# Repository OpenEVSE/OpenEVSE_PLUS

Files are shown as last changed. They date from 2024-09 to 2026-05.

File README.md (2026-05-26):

# OpenEVSE_PLUS
README.md for OpenEVSE Hardware
Files SCH and BRD in Eagle format
License CC BY-SA 3.0
OpenEVSE Hardware

Current Version OpenEVSE_PLUS_v6.5.1.

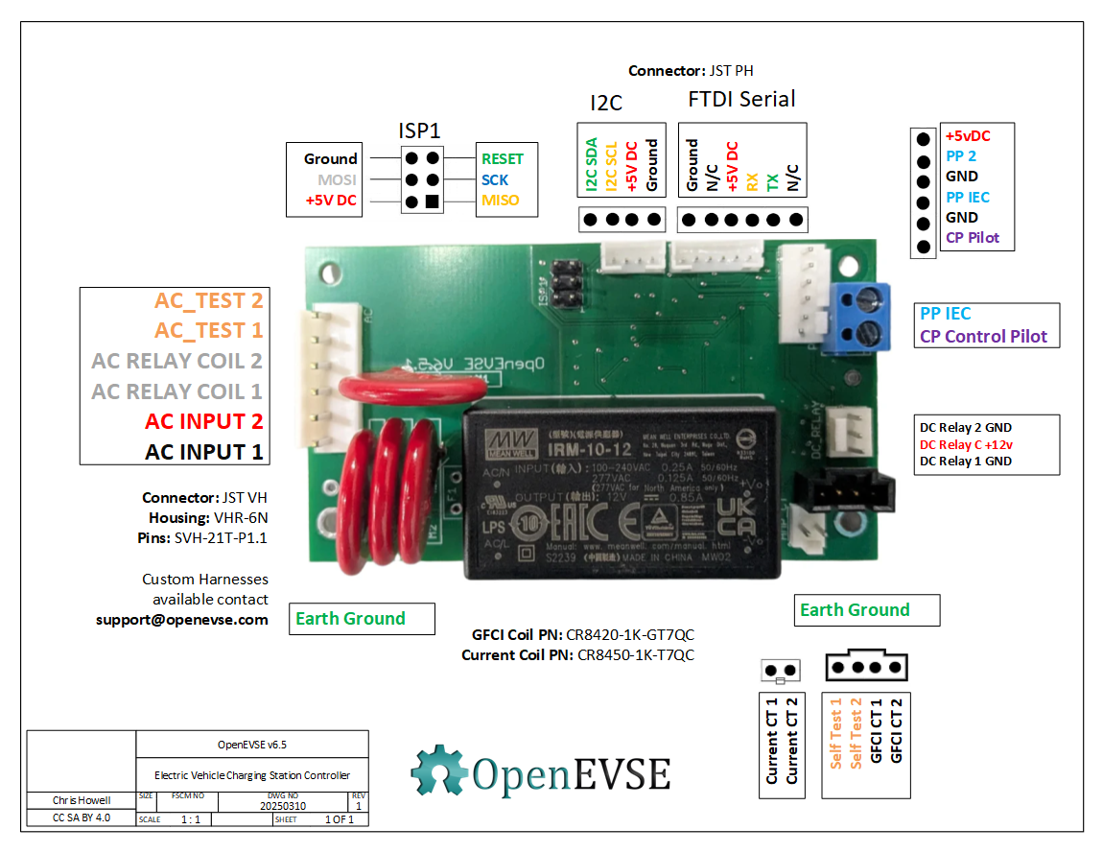
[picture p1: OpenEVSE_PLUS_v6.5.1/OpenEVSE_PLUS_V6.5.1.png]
OpenEVSE Electric Vehicle controller v5.5 SAE J1772 IEC 61851


OpenEVSE_PLUS_V6.5 - New more powerfull 10 watt Power supply (v5.5 and below 4 watt) with support for 277V AC and higher 85C operational temperature. Reworked AC detect circuits to support new UL requirement for "Continuous" Ground Monitoring vs "While Charging". Pulled ADC6 HIGH to auto detect CGMI requirement. Added on-board Surge supression MOVs. Added connector with Pilot, Proximity Pilot, Ground and 5v.

OpenEVSE Electric Vehicle controller v5.5 SAE J1772 IEC 61851

OpenEVSE_PLUS_V5.5 - Moved GFCI Test pin to enable move of DC Relay outputs to PWM capable pins supporting full power closing reduced power holding in OpenEVSE 7.1.2+ firmware. Pulled PD7 HIGH to auto detect board version in software to automatically set new/old pin values without requiring different firmware. Replaced 0.1" generic non-polarized connectors with JST PH for Serial (WiFi) and i2c (Display). Combined power and data connections for WiFi to reduce eliminate a screw terminal connector and simplify wiring harness. Replaced DC/DC converter with a TC1044S invert chip to generate -12v from +12v. 

OpenEVSE Electric Vehicle controller v5 SAE J1772 IEC 61851

OpenEVSE_PLUS_v5 - Optimized for reduced build time and high volume manufacturing of changing stations, removed most screw terminals and replaced with common connectors. Change from 2 single chanel opto-isolators for AC detection to 1 dual channel. Added ground connections to screw holes.

OpenEVSE Electric Vehicle controller v4 SAE J1772 IEC 61851

OpenEVSE_PLUS_v4 - Has 2 AC Detect chips like v1 + v2 plus the AC relay driver of v3. Added rectifier diodes to AC detect to improve detection in some conditions. Changed GFCI to individual pinout 4 pins.

OpenEVSE_PLUS_v3 - Removed 1 AC Detect chip and added AC relay driver. Added Current measurement circuit

OpenEVSE_PLUS_v2.5 - Added Current measurement circuit.

OpenEVSE_PLUS_v2 - modified GFCI pinout

OpenEVSE_PLUS_v1 - Inital version - Combined OpenEVSE v7 board and Advanced power supply into single board

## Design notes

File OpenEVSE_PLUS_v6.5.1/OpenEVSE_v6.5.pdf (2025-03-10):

## I2C FTDI Serial ISP1

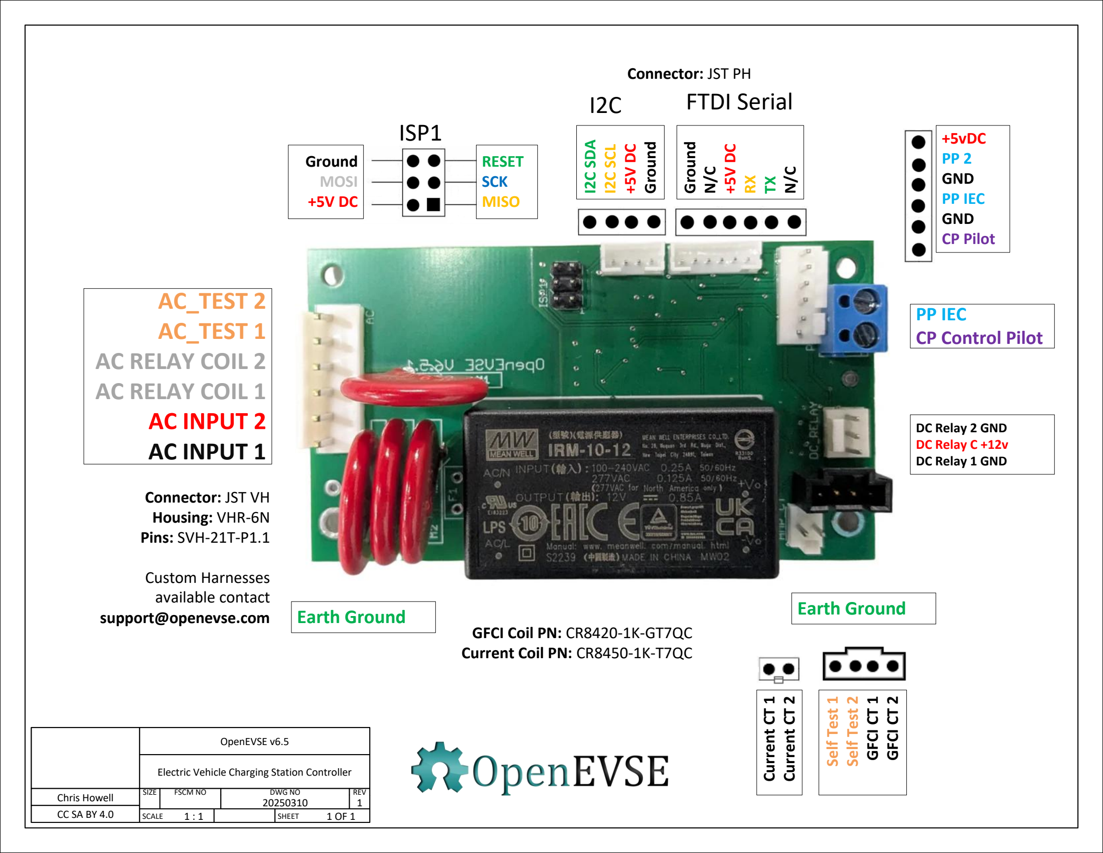
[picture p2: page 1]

Chris Howell Chris Howell | SIZE SIZE | FSCM NO FSCM NO | DWG NO DWG NO | REV REV
| | | 20250310 20250310 | 1 1
CC SA BY 4.0 CC SA BY 4.0 | SCALE SCALE | 1 : 1 1 : 1 | | SHEET SHEET | 1 OF 1 1 OF 1

OpenEVSE v6.5

Electric Vehicle Charging Station Controller

OpenEVSE v6.5

Electric Vehicle Charging Station Controller

## AC_TEST 2 AC_TEST 1 AC RELAY COIL 2 AC RELAY COIL 1 AC INPUT 2 AC INPUT 1

PP IEC
CP Control Pilot

Earth Ground Earth Ground

DC Relay 2 GND
DC Relay C +12v
DC Relay 1 GND

I2C SDA
I2C SCL

+5V DC

Ground

Ground

N/C

+5V DC

RX
TX

N/C

RESET
SCK
MISO

Ground
MOSI
+5V DC

Current CT 1

Current CT 2
Self Test 1

Self Test 2

GFCI CT 1

GFCI CT 2

Connector: JST VH
Housing: VHR-6N
Pins: SVH-21T-P1.1

Custom Harnesses
available contact
support@openevse.com
GFCI Coil PN: CR8420-1K-GT7QC Current Coil PN: CR8450-1K-T7QC

+5vDC
PP 2
GND
PP IEC
GND
CP Pilot

Connector: JST PH

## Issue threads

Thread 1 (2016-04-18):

Pilot power supply voltages are not shown or shown wrong, improvements recommended

jerkey, 2016-04-18:
IC4, the op-amp in the Pilot section, is shown with its negative power supply pin labeled "GND" but it is actually connected to VOUT- from the DCDC converter, whose GND is connected to actual GND of the circuit.  Neither VOUT- nor VOUT+ are labeled with voltages, but I was able to look up the DCDC power supply "D107E" and find out that it produces -12 and +12 volts from a FIVE volt input supply.

However, "DCDC" the D107E is shown in the schematic to be powered with +12v (coming from U$1 the AC-DC power supply) which would fry it if you try it.  Since the part called "TVS" is a 13.6v Zener diode (I had to look this up) there is really no need for a seperate DCDC converter...

I recommend deleting most of the parts inside the "Pilot" box and using instead an IXDD604PI mosfet driver chip, which you power directly from the +12v supply from the AC-DC power supply.

I would update the schematic but I use KiCAD not Eagle so I would have to start over.

Thank you for publishing this design.

chris1howell, 2016-04-19:
Deleting the DCDC and circuitry is not possible, SAE J1772 requires the pilot signal to operate at +12v HIGH and -12v LOW. The charging station to verify an EV is present, which is performed by a "diode check" at -12v. Several SAE J1772 error stated require the pilot to be pulled to -12v.

The bi-derectional TVS +13.6 and -13.6 is for surge, static and other transient spikes not for voltage regulation.

Part D107E (for 5v input) and D117E (for 12v input) were discontinued several years ago. The current OpenEVSE PLUS v4 uses part MD112D-12 in the Bill of Materials.

The recommended modifications and MOSFET driver would result in a non-compliant SAE J1772 pilot signal. The current design is mature and fully complaint with 100% compatibility on all vehicles tested.

Closed 2016-04-19.

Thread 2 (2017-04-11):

Bill of materials not ok?!

micdre, 2017-04-11:
Hello,

I found out that the BOM list, genretated in Eagle, is not ok in version 4 and 3! (maybe other versions too)
Is there somewhere a good list.

Regards, Michel

chris1howell, 2017-04-11:
I will take a look at the Eagle generated BOM. Any information on what parts are not okay?

micdre, 2017-04-11:
Hello
Thanks!

IC2 is not a mega 8 but a 328P
IC3 is not a LMV358 but a LM358
IC4 is not a LMV358 bu a LF353
Maybe there's more...

Costs me a couple of parts....

Regards, Michel

Verstuurd vanaf mijn iPhone

Op 11 apr. 2017 om 21:39 heeft Chris Howell <notifications@github.com<mailto:notifications@github.com>> het volgende geschreven:

I will take a look at the Eagle generated BOM. Any information on what parts are not okay?

—
You are receiving this because you authored the thread.
Reply to this email directly, view it on GitHub<https://github.com/OpenEVSE/OpenEVSE_PLUS/issues/2#issuecomment-293377590>, or mute the thread<https://github.com/notifications/unsubscribe-auth/AaAt5OanwKMKgq3p1027xw1ZBOK7_In8ks5ru9btgaJpZM4M5xZF>.

chris1howell, 2017-04-11:
I updated the following part values so generic footprints report the correct part when exporting Eagle generated BOM.

IC2 value 328P
IC3 value LM358
IC4 value LF353
TVS value P6SMB16CA
D1 value AZ23C5V6-7-F

micdre, 2017-04-11:
In wich version of the board?

Verstuurd vanaf mijn iPhone

Op 11 apr. 2017 om 22:07 heeft Chris Howell <notifications@github.com<mailto:notifications@github.com>> het volgende geschreven:

I updated the following part values so generic footprints report the correct part when exporting Eagle generated BOM.

IC2 value 328P
IC3 value LM358
IC4 value LF353
TVS value P6SMB16CA
D1 value AZ23C5V6-7-F

—
You are receiving this because you authored the thread.
Reply to this email directly, view it on GitHub<https://github.com/OpenEVSE/OpenEVSE_PLUS/issues/2#issuecomment-293384871>, or mute the thread<https://github.com/notifications/unsubscribe-auth/AaAt5Kc0vCaPSEjiRwvulRwJArvykdhDks5ru91lgaJpZM4M5xZF>.

chris1howell, 2017-04-11:
V4.

On Apr 11, 2017 1:26 PM, "micdre" <notifications@github.com<mailto:notifications@github.com>> wrote:
In wich version of the board?

Verstuurd vanaf mijn iPhone

Op 11 apr. 2017 om 22:07 heeft Chris Howell <notifications@github.com<mailto:notifications@github.com><mailto:notifications@github.com<mailto:notifications@github.com>>> het volgende geschreven:

I updated the following part values so generic footprints report the correct part when exporting Eagle generated BOM.

IC2 value 328P
IC3 value LM358
IC4 value LF353
TVS value P6SMB16CA
D1 value AZ23C5V6-7-F

—
You are receiving this because you authored the thread.
Reply to this email directly, view it on GitHub<https://github.com/OpenEVSE/OpenEVSE_PLUS/issues/2#issuecomment-293384871>, or mute the thread<https://github.com/notifications/unsubscribe-auth/AaAt5Kc0vCaPSEjiRwvulRwJArvykdhDks5ru91lgaJpZM4M5xZF>.

—
You are receiving this because you modified the open/close state.
Reply to this email directly, view it on GitHub<https://github.com/OpenEVSE/OpenEVSE_PLUS/issues/2#issuecomment-293389832>, or mute the thread<https://github.com/notifications/unsubscribe-auth/ABvYH50hh1Q3WBz-j6e3Ijn0WjQ5jKeUks5ru-HxgaJpZM4M5xZF>.

micdre, 2017-04-11:
Thanks!

Verstuurd vanaf mijn iPhone

Op 11 apr. 2017 om 22:34 heeft Chris Howell <notifications@github.com<mailto:notifications@github.com>> het volgende geschreven:

V4.

On Apr 11, 2017 1:26 PM, "micdre" <notifications@github.com<mailto:notifications@github.com><mailto:notifications@github.com>> wrote:
In wich version of the board?

Verstuurd vanaf mijn iPhone

Op 11 apr. 2017 om 22:07 heeft Chris Howell <notifications@github.com<mailto:notifications@github.com><mailto:notifications@github.com><mailto:notifications@github.com<mailto:notifications@github.com>>> het volgende geschreven:

I updated the following part values so generic footprints report the correct part when exporting Eagle generated BOM.

IC2 value 328P
IC3 value LM358
IC4 value LF353
TVS value P6SMB16CA
D1 value AZ23C5V6-7-F

—
You are receiving this because you authored the thread.
Reply to this email directly, view it on GitHub<https://github.com/OpenEVSE/OpenEVSE_PLUS/issues/2#issuecomment-293384871>, or mute the thread<https://github.com/notifications/unsubscribe-auth/AaAt5Kc0vCaPSEjiRwvulRwJArvykdhDks5ru91lgaJpZM4M5xZF>.

—
You are receiving this because you modified the open/close state.
Reply to this email directly, view it on GitHub<https://github.com/OpenEVSE/OpenEVSE_PLUS/issues/2#issuecomment-293389832>, or mute the thread<https://github.com/notifications/unsubscribe-auth/ABvYH50hh1Q3WBz-j6e3Ijn0WjQ5jKeUks5ru-HxgaJpZM4M5xZF>.

—
You are receiving this because you authored the thread.
Reply to this email directly, view it on GitHub<https://github.com/OpenEVSE/OpenEVSE_PLUS/issues/2#issuecomment-293391892>, or mute the thread<https://github.com/notifications/unsubscribe-auth/AaAt5HFzgKjKpxOICllg82zijdx22NiBks5ru-PFgaJpZM4M5xZF>.

Closed 2017-04-11.

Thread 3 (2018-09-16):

D8 Diode type

mr-const, 2018-09-16:
I found out in the BOM, that D8 diode value is 1N4004, but "device" name is  MBRA340T3, so it's not clear which one is valid, or they both can be used (1N4004 is 400V diode, however 340 is 40V only)

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

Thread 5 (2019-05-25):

Math / Theory of the GFCI circuit

RyanCopley, 2019-05-25:
I did find the theory of operations, and I reviewed the burden resistor calculator, but I am at odds with trying to understand how a burden resistor of 412 ohms was selected.

For the CT being used (http://www.crmagnetics.com/Assets/ProductPDFs/CR8400%20Series.pdf) it has the specs
Max RMS Current / Ir = 20 amps
Current Sensor turn ratio / Te = 1011:1
The arduino System Voltage is 5v

I plug these values in to https://tyler.anairo.com/projects/open-energy-monitor-calculator and I get a burden resistor of 89 ohms. Are you scaling down the max RMS current to ~4.3 amps for more sensitive detections?

Could you also go into explaining what the first OP Amp is for? I understand why the second one exists, but the first is elusive to me. My current guess is that it's being used as memory to keep an unbalanced current to remain a high value even whilst it oscilates

I would really appreciate the help understanding the theory here :-)

chris1howell, 2019-05-26:
The coil is scaled way down, there is no point reading anything over 20ma.
Sensitivity to low currents is more important.

The first stage of the Opamp is a amplifier or multiplyer. The input which
is a very tiny voltage is amplified before hitting the second stage which
is a voltage comparator. If the amplified voltage from the coil is above
the threshold the output of the opamp goes high. The Inturupt on the
microprocessor is triggered on the rising voltage of the opamp output.

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

RyanCopley, 2019-05-26:
Thank for you for the explanation, that is really helpful!

Closed 2019-05-26.

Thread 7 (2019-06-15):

Suggestion

jbakuwel, 2019-06-15:
Replace contactor with something like https://www.digikey.com/product-detail/en/sensata-crydom/D24125/CC1143-ND/254192

Zero-cross might also be nicer for the car charger....?

chris1howell, 2019-06-15:
Solid State Relays are not a good fit for EVSEs for 3 main reasons. The
main purpose of the EVSE is isolation until all safety checks pass. SSRs
can not guarantee isolation and there is a chance of shock even when
commanded off. Additionally EVSEs must fail safe. SSRs tend to fail closed
shorted where the mechanical properties of a relay tend to fail safe.

Additionally, SSRs have a pretty high internal resistance, at a high
sustained current this can translate into hundreds of watts of waste heat,
far too much to deal with in a small enclosure.

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

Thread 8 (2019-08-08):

Non OpenESVE LCD

samigroup, 2019-08-08:
Hello,
I am experiencing around with the OpenEVSE Plus Controller, I have added my available LCD 16X2, with pack module for I2C is there any way to update the I2C address without flashing the OpenEVSE controller code?
-- I know the LCD through the OpenEVSE is jumped A0-A2, so I soldered the A0-A2 jumpers to get the same address,  but its not just that, its more, where its two different communication schemes. But its protected for throught the header files and headers, I was wondering if I can change the selection of LCD definition/I2C header through the RPI interface (wifi interface)

- I am not using the RTC, nor the Temperature, ( disabled them through wifi interface)

samigroup, 2019-08-26:
If anyone was successful with this, it would be great if you can give me some pointers. Thanks!

chris1howell, 2019-08-26:
To use a different LCD/Controller combo you will need to modify the source
code to support your particular device and recompile.

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

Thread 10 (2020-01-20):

Suggestion for PP

giorgio80, 2020-01-20:
Dear,

I'm trying to maker hobby a board but it's  It's not clear pp specification. I better explain.
In particular,  it's clear for me how pp work,  simply reading resistance state to understand supported cable power and car presence,  but is not clear if it has to be 5v for specification.

I better explain.
I see it is connected to 5v then to add for reading inout.  My board works on 3.3v   so my question is :  would 3.3v setup would work or pp has to be 5v for j1772 specific ?

thanks.

sauttefk, 2020-01-20:
You can also use just 3.3V for your circuit. You just have to measure the resistance.
5V was the standard voltage of digital circuits back in the time, J1772 was standardized.

But 5V will have a higher noise immunity than just 3.3V, but i don't think that matters, as the resistance to measure is low enough (the current high enough).

Make sure to protect your PP input circuitry against static discharge and  leakage current due to wet/dirty ev-connector/short circuit to CP.

giorgio80, 2020-01-21:
Thanks for your answer, really more clear now . About checking the value can I also ask you when in the charging process it has to be checked ?
Thanks again :)

sauttefk, 2020-01-22:
You are developing a device that has a lot of inherent life threatening electrical safety risks!
Of course you have to monitor all values continuosly and shut off the power immediately when any parameter exceeds acceptable limits.
Maybe you should invest in getting the IEC61851 standard from ISO.

giorgio80, 2020-01-23:
hi @sauttefk
sorry I was not clear.  it's clear this has to be monitored continuously especially for overcurrent, real question was when PP has to be checked initially ,  I suppose immediately after pilot start ( and adapting load consequently) .  is this a right approach? I read around some other say that no Pwm pilot has to be started before pp is checked other instead say to start Pwm and continuously check for pp and to stop (without open contactor) charge process if no certified cable is detected.

Niko-La, 2020-01-30:
Make sure to protect your PP input circuitry against static discharge and leakage current due to wet/dirty ev-connector/short circuit to CP.

@sauttefk can you please elaborate on this.  Does openevse already do this in the schematic.

Also where can I follow the work being done for OpenEvse v6

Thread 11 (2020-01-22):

Incorrect GFCI self-test current?

davidrea, 2020-01-22:
The V5 schematic has a 330Ω resistor and 5V drive signal, resulting in a 0-15.15mA square wave through the self-test winding. The [CT product page](https://store.openevse.com/collections/all-products/products/gfci-current-transformer) indicates a trip current of 15-20mA, and a 5-turn self-test coil.

Should the resistor on the board actually be 1.6KΩ so that you only get 3mA through the self-test primary winding? In this case the voltage seen from the GFCI CT would be 5x that, since the nominal "pass the load wires through" case is a 1-turn primary. This would run the self-test at a current transfer ratio much closer to the design-intent in-use threshold.

(It's also understandable that there could be some CTR loss due to the crest factor of the square wave drive signal; the closest-to-ideal CTR would be with a sinusoidal input, so this might need to be derated a bit.)

chris1howell, 2020-01-22:
The UL current maximum for the test is 30ma. The test signal is not solid DC but PWM, the duty cycle is set to stay under the maximum.

UL has tested this setup with Wattzilla in the OpenEVSE v4 and are satisfied with the theoritialcal and tested levels.

Chris

On Wed, Jan 22, 2020, 1:40 PM Dave Rea <notifications@github.com<mailto:notifications@github.com>> wrote:

The V5 schematic has a 330Ω resistor and 5V drive signal, resulting in a 0-15.15mA square wave through the self-test winding. The CT product page<https://store.openevse.com/collections/all-products/products/gfci-current-transformer> indicates a trip current of 15-20mA, and a 5-turn self-test coil.

Should the resistor on the board actually be 1.6KΩ so that you only get 3mA through the self-test primary winding? In this case the voltage seen from the GFCI CT would be 5x that, since the nominal "pass the load wires through" case is a 1-turn primary. This would run the self-test at a current transfer ratio much closer to the design-intent in-use threshold.

(It's also understandable that there could be some CTR loss due to the crest factor of the square wave drive signal; the closest-to-ideal CTR would be with a sinusoidal input, so this might need to be derated a bit.)

—
You are receiving this because you are subscribed to this thread.
Reply to this email directly, view it on GitHub<https://github.com/OpenEVSE/OpenEVSE_PLUS/issues/11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>, or unsubscribe<https://github.com/notifications/unsubscribe-auth/AAN5QH3ZUFWEQT7AV622SYTQ7CHKFANCNFSM4KKKRWNA>.

davidrea, 2020-01-23:
Excellent, thanks for the clarification!

Closed 2020-01-23.

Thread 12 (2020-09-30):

GFCI tripping point.

faustomilletari, 2020-09-30:
Dear community,

According to this thread https://www.google.com/url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

there are changes in the regulation that require the GFCI to be more sensitive to current leakages. It seems that the current OpenEVSE hardware is built to have the GFCI trip at 15mA, whereas regulation requires 6mA.

I understand that changing the tripping point requires changes in the resitors used as burden resistor etc. I would like to ask you if
1) you think the current circuit can be adapted to the new requirements by swapping resistors
2) the new 6mA limit is high enough not to cause any issues with false positive tripping signals

I would like to state that i'm not an expert, and therefore i am still learning a lot. if i have misstated something in this issue please let me know and feel free to close it.

If also you could help me make calculations for new resistor values for the GFCI, in the sense of pointing me to material that can help me understand how that circuit works, i would be very grateful!

sauttefk, 2020-09-30:
**Caution:**
The current transformer used with OpenEVSE does not protect from **DC** fault currents.
Due to the fact that it is a coil around the conductors it can only pick up **AC** currents.

AC tripping current has to be at most 30mA
DC tripping current has to be at most 6mA

To achieve this you either need a Type B GFCI or a Type A GFCI plus something like the [WA RCM14-03 AC/DC Residual Current Monitor](https://deltrixchargers.com/wp-content/uploads/2019/10/WA-DS-015-RCM14-03-Rev-B.pdf).

A [hall effect sensor](https://en.wikipedia.org/wiki/Hall-effect_sensor) - in contrast to a current transformer coil - can detect DC current.

faustomilletari, 2020-09-30:
I am confused as of why this is needed at all... For a "normal" single or three-phase charging station where would we see this DC current coming from? The only place with DC current is the board itself and the pilot.

is this regulation meant to be applied by DC charging stations?

sauttefk, 2020-09-30:
A DC ground fault can occur, when a ground fault occurs behind the rectifier i.e. a battery pole has connection to earth.

faustomilletari, 2020-09-30:
Yes. now i understand. I am reading about it in this interesting article which says exactly what you stated in your last answer. http://www.mastrogippo.it/2019/09/rcm-direct-current-sensing-how-its-done/

thank you for helping me. It seems like this system is not required for EVSE meant to be home chargers for private use. So i think it might not be needed in my case...

thanks

SDCSolutions, 2020-09-30:
Looks like it is for the IEC62196 standard which governs CCS or DC charging. Also hence the loss of ground detect in the spec. http://www.doepke.co.uk/download/Techpub-06.pdf

Get Outlook for iOS<https://aka.ms/o0ukef>
________________________________
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

sauttefk, 2020-09-30:
**Attention:**
A DC ground fault can also occur with AC charging. A connection of the HV-battery to the chassis can easily happen e.g. a marten chewing on cables or rubbed through cables.

SDCSolutions, 2020-09-30:
So would that type of RCD need to be mounted on the ground line?

Get Outlook for iOS<https://aka.ms/o0ukef>
________________________________
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

sauttefk, 2020-09-30:
An affordable Type B RCD is this [GEYA GYL9 63A 30mA](https://de.aliexpress.com/item/33020060308.html)
An RCD is your life insurance when something bad happens to your EVSE / cable / connector / car in this wet, hot, cold, dirty environment you are going to deliver deadly voltages.

sauttefk, 2020-09-30:
When you do a 240V 2phase charging in North America, a 4 pole RCCB has to be used, leaving on pole unconnected (N/L1/L2/nc).

SDCSolutions, 2020-09-30:
Frank,
I guess my question is how is an RCD supposed to protect against a vehicle fault. Most of these control systems are designed to protect against unwanted electricity leaving the EVSE via the plug.

If I am understanding you correctly, this legislation is designed to protect against energy leaving the car?

Or is this in the event of a poorly set up solar panel installation?

Get Outlook for iOS<https://aka.ms/o0ukef>
________________________________
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

sauttefk, 2020-09-30:
A RCD monitors if any current sent out on one conductor does not return on any other conductor, but goes another way to earth. In the worst scenario through your heart.
So any insulation fault behind causing a current to earth, trips the RCD and therefore protects life and property.

A RCD can also be used to automatically isolate a faulty solar panel installation.

SDCSolutions, 2020-09-30:
Hi Frank,
I’m just trying to identify the source of the hazard here, the device that is being protected and the rationale of using it in a level 2 product.

If the source of the hazard is the vehicle, the RCD in the EVSE  is designed to protect the house?

I can understand the RCD being necessary for a solar panel, but then I question the rationale behind making the legislation around the EVSE as opposed to the solar panel.

If the hazard is the utility sending DC power,  along the same lines as the AC power, then I guess I would consider that a potentially valid risk. Not sure how it would happen as substations are usually all transformers where I live and it’s a little difficult to pass DC through them, but if I want to be protected from bad actors or negligent installations, why not make every plug an RCD circuit and leave the expensive hardware out of the EVSE.

Fundamentally, my question is why is this necessary to be put on a product people are already complaining is too expensive?

Get Outlook for iOS<https://aka.ms/o0ukef>
________________________________
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

sauttefk, 2020-10-01:
The International Electrotechnical Commission Standard [IEC 60364-7-722](https://webstore.iec.ch/publication/29958) demands either a 30mA Type B RCCB or a special Type EV (30mA AC/6mA DC) RCCB.

I don't know the legal requirements all over the world. But at least in Europe this is legally binding (every new installation has to obey these standards otherwise the electrician and/or the operator are liable for any damage or harm).
As far as I know these standards also apply to North Amerika.

chris1howell, 2020-10-01:
The standard in most of the world including USA is CCID 20. Which is AC
detection of ground fault at 20ma +0ma -5ma, so effectively the trip is
somewhere between 15ma and 20ma. There is no requirement for DC.

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

faustomilletari, 2020-10-02:
Hello,
thank you chris for your inputs.

I still hear conflicting opinions about this. I have found a component (datasheet here https://vacuumschmelze.com/Assets-Web/4641-X900.pdf) which has the desired functionality and is specifically built for EVSE.

Putting this component in the current design of OpenEVSE would mean to gut the GFCI portion of the circuit and simplifying it. Apparently PIN3 of the device linked above is low as long as there is no fault and goes in high-impedence whenever there is a system fault or a DC current >= 6ma or a AC current >= 30ma.

We could remove everything and add a pull up resistor to the GFCI_INT line connected directly to the pin 3 of the GFCI fault device linked above.

For what concerns tests. the devices wants to sense pin number 1 low (GND) for any time between 30ms to 1.2 sec to trigger testing. I would imagine GFCI_TEST line is active high, so i was thinking to put a NOT gate in tail of that line (with a pull up resistor just to make sure), and drive the PIN1 of the GFCI device with that.

The GFCI device absorbs around 35mA to function. Therefore i feel we can connect it to +5V and GND in the board.

Do you think such a change would work. I am NOT knowledgeable in terms of electronics, i'm improvising. i'm awaiting you expert opinion!

Fausto

faustomilletari, 2020-10-02:
Something like this? (I'm really confident this WON'T work)

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

sauttefk, 2020-10-02:
@faustomilletari  [benvac 4641-X900](https://vacuumschmelze.com/Assets-Web/4641-X900.pdf) is a very interesting part, but not cheap (~80USD ). Seems to be a product developed by Vaccumschmelze (ferrite and magnets) and [Bender](https://www.bender.de/produkte/differenzstrom-ueberwachung/rcmb121) (electrical safety products). The product name benvac stongly suggests this.

But [WA RCM14-03](https://www.stegen.com/en/ev-products/126-residual-current-sensor.html) seems to be cheaper (~60 USD) and easier to connect.

faustomilletari, 2020-10-03:
In that case, with WA RCM14-03, we would directly connect the GFCI_INT (active high) to the fault pin and GFCI_TEST (active high) to the test pin. The power supply would be directly the +12 GND form the AC/DC unit.

Great!

sauttefk, 2020-10-05:
[KEMET FG-R05-3A](https://content.kemet.com/datasheets/KEM_SE0217_FG.pdf) is also a possible AC/DC ground leakage current sensor (~60USD).

jackpotdk, 2020-11-16:
Aha!! @faustomilletari , I am sitting with the exact same challenge here.
I am currently looking at https://www.bender.de/en/products/residual-current-monitoring/rcmb121

Have you made any progress on the matter?

DeltaVetal26, 2020-12-03:
Hi all,

There is a similar sensor from Stegen Electronics (Netherlands).

https://www.stegen.com/en/ev-products/126-residual-current-sensor.html
It combines DC (6mA) and AC (30mA) leakage protection.

The only thing is that it requires an external 12V power supply and a logic level (for communicating with the controller) also 12V.

There are several options:

1) There is an I2C bus on the OpenEVSE board, which is not used, but its pins are on the terminal. In the firmware, you can configure these pins for input-output and connect a sensor to them (if the one that I suggested is through a voltage divider (for example, an optocoupler). It is impossible without a divider, since the microcontroller is not designed for 12V from the sensor.

 Then just read the state of the sensor pin. If a leakage occurs, the sensor will change the state of the line, we will see it and will be able to stop charging.

2) If you have OpenEVSE together with ESP (WiFi), you can also connect the sensor to it (via a divider). In it, poll the status of the sensor and, in the event of a leak, send a RAPI command to OpenEVSE to stop charging. But here you need to make sure that the ESP always has a connection with OpenEVSE in order to be ready to stop charging.

Closed 2020-10-02.

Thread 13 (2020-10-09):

e-Golf Charging keeps starting/stopping

arnolde, 2020-10-09:
I have a 2020 VW e-Golf since April 2020 (new) and have been charging it since May with OpenEVSE with 2 phases (it has a 7.2kW onboard charger), it worked fine until about a week ago, then the car was only charged sometimes, with interruptions. Today I sat down and finally had time for an extensive diagnosis, and I see the following:
a) once in a while I see "diode check failed" on the OpenEVSE webUI page (without the cable having been touched - when I soft-reset the EVSE with the RAPI command, it starts working again)
b) when no error is displayed, the car charges for about 10 seconds and then pauses for 10-30sec (the only way I see that is by logging the power meter every second and watching the current in realtime) - there is no regular pattern though, and it seems not to change behaviour when I change the charge current between 6/10/16A in the webUI - see the many narrow, square spikes in the image (ignore the long steady part in the left half, that is not the car)

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

c) after about 5 tries the car seems to stop trying to charge

The car's smartphone app sometimes says "I'm sorry, there was an error of some sort, and charging stopped". If I click on "start charging" then it starts (a new sequence of atempts) again.

If I charge the car with VW's own 230V-charger (ICCB) it charges fine.

The only other info I have, is that a couple months ago the openEVSE type 2 plug got wet (the cap was on, it was dangling with the cap downwards, it got rained on, which collected inside the cap) and the CP pin got corroded. I cleaned it a little and charging worked again, reliably, until about 1 week ago. When I started diagnosing the charging problem this morning, I cleaned it thoroughly, but it did not improve this whole issue.

It almost seems to me like the car's firmware was updated a week ago (over the air, without my knowledge) and now it doesn't work well anymore with openEVSE? Is that possible?

arnolde, 2020-10-11:
@chris1howell Maybe I should have opened this under open_evse ? I'm sorry I'm not sure where exactly the right place for such an issue is.

Is there a way to read a debug log in realtime (like per UDP broadcast i.e.) so I can see if the openEvse is even detecting the interruptions at all? (I don't have current sensors installed) - then I could be reasonably sure that the car is causing it, unless the PWM is failing for some reason...

chris1howell, 2020-10-11:
Github issues are generally for bugs in coding or errors in design. Support
requests should be sent to support@openevse.com.

A. Diode check error while unplugged sounds like water in the handle making
connection from pilot to ground. This could also cause GFI errors.

B. This issue sounds like a poor CP or ground connection or power is not
detected by the vehicle when the relay closes. Ensure the relay is closing
properly and power is provided to the vehicle.

On Sun, Oct 11, 2020 at 5:26 PM Ethan Arnold <notifications@github.com>
wrote:

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

arnolde, 2020-10-12:
Thanks! The diode check does not fail when unplugged, only once in a while when trying to charge. I have GFCI disabled since I don't have a GFCI transformer mounted, I rely on my 30mA GFCI in my house's main distributor box.

I guess I will have to monitor the PWM and relay contacts and report back with those results.

Is there really no event log with timestamps I could access, so I can see if there were any rapidly changing events I'm missing on the ESP webUI?

arnolde, 2020-10-29:
Just to conclude with this problem: I opened up the type 2 plug handle and found water drops inside. Apparently the plug was not watertight :-( after drying out everything for a couple days indoors and then with a hairdryer to be sure, I reassembled everything and it now works again. My suspicion is that the e-Golf EV detected false currents somehow and interrupted the charging.

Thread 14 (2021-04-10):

Advanced_v5_2020.pdf missing power regulator

kallisti5, 2021-04-10:
@chris1howell   The new Advanced_v5_2020.pdf diagram is missing the power regulator. It shows 12v connected to 5v directly

chris1howell, 2021-04-10:
The power regulator is not missing. The new (February 2020) OpenEVSE ESP32
WiFi board has a built in 12v to 3.3v DC/DC converter. It is much more
efficient and simple to wire than the previous UBEC/Huzzah setup with
external 12v to 5v converter and onboard 5v to 3.3v regulator.

On Sat, Apr 10, 2021, 6:06 PM Alex von Gluck IV ***@***.***>
wrote:

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

kallisti5, 2021-04-10:
oh.. Nice!  I just put the newer Feb 2020 board into my OpenEVSE and wired the wifi module up to the existing DC/DC converter.  Guess I need to crack it open and simplify a bit :-)

kallisti5, 2021-04-10:
although... the diagram does show 5v input pins on the wifi module which makes it a bit more confusing...
https://github.com/OpenEVSE/OpenEVSE_PLUS/blob/master/OpenEVSE_PLUS_v5/Advanced_v5_2020.pdf

SoDi1203, 2021-04-20:
hi, is this a broken link?
https://github.com/OpenEVSE/OpenEVSE_PLUS/blob/master/OpenEVSE_PLUS_v5/Advanced_v5_2020.pdf

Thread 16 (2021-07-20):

Connect LED to Open EVSE with free pin

DylanVautrin, 2021-07-20:
Hi !
After looking at this issue : https://github.com/lincomatic/open_evse/issues/98
I tried to connect RGBLED to open evse without I2C, so after looking for free pin , i've undefined the RGBLCD to use pin of the LCD in first time, but when i try to write a HIGH/LOW levels on pin SDA, the Open EVSE restart continually.
I used the shortcut "SDA" in the code.
Maybe i do something wrong, someone have a solutions or a different way to proceed ?
Thanks
PS: I just do a digitalWrite(SDA,HIGH);

Closed 2021-07-20.

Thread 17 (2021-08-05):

5.5 board support additional j1772 output?

sroskelley, 2021-08-05:
Seems like this board could support an additional j1772 with no new parts to the board.

posit1: Board already supports two dc contactors?
posit2: PP pin is connected to a pwm?
posit3: risk doesn't increase with this feature.

examples scenerios, A, B ,C.. pilot1 is PLT.. pilot2 is PP
Say controller is configured for <=32amp output for this example.
A, state: 0 cars connected.
A, contactor1, off
A, contactor2, off
A, pilot1: allows 16 amps
A, pilot2: allows 16 amps

A->B
B, car is connected to pilot1. Requests 16amp (per pilot advertisement)
B, contactor1, on
B, openevse detects amprage draw of ~16
B, pilot2 gets set to 1amp allowed.
B, pilot1 gets set to 31amp allowed.
B, contactor2, stays off

B->C
C, car gets connected to pilot2. Reqests 1amp  (per pilot advertisement)
C, pilot1 gets set to 16amp allowed.
C, wait for monitored amperage to be reflected to <16amps before enabling c2.
C, pilot2 gets set to 16amp allowed.
C, contactor1, on
C, contactor2, on

In all scenarios if amperage is ever detected to be over.. cut all contactors(just like now)

The only new part needed for the kit would be a contactor and j1772 assembly. No additonal coils. second j1772 would flow through same current sensors but differnet contactor.

I assume I'm missing something safety wise.. Sorry for wasting everyones time, unless someone learns something, then I regret nothing.

Side question.. is there there a reason we wouldn't move the coils to be on the input instead of the output of the 5.5 diagram

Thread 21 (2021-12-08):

Stuck relay

kallisti5, 2021-12-08:
Hey, the stuck relay detection works :-)

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

Had the 50A Struthers - Dunn contactor weld itself running at 32A.   Anyone else have issues like that?  The relay is only around a year old.

kallisti5, 2021-12-08:
Looks like a few other people have seen this:
https://groups.google.com/g/openevse/c/4wFzy82jwYo

kallisti5, 2021-12-08:
I lightly took a file to the contacts, then sanded with 400 grit, 2000 grit, and scrubbed the contactor with contact cleaner.
30A after 5 or 10 minutes and everything seems fine again without any excessive heat

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

We might want to add cleaning the contactor to yearly maintenance or something

kallisti5, 2021-12-08:
I'm working on a contactor maintenance guide here:
https://openevse.dozuki.com/Guide/Contactor+maintenance/40

I need to get a few more pictures together before it's ready to publish

kallisti5, 2021-12-08:
Published.  I changed the language from Contactor to Relay.  *Technically* these are more contactor-like vs relay-like, but the datasheet calls them relays... so I digress :-)

https://openevse.dozuki.com/Guide/Relay+Maintenance/40?lang=en

Closed 2021-12-08.

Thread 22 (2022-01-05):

CCS-Type 2 DC from DC Power?

JohnGalt1717, 2022-01-05:
Hi, I'm building a DC Bus design that skips the entire inverter process. Is there any documentation on using DC fast charging with this project?

Basically what I'm looking at doing is using this, if possible to charge from a LiFePO4 battery + solar directly DC with a small DC/DC synchronous boost converter (at over 98%) which will cost about 1/8th the cost of a dc/ac converter and eliminate all of the losses from DC/AC and then back AC/DC in the car. The synchronous boost converter is easy (going for 384VDC) and I've built one. The harder stuff that is more risky is to talk to the car and now blow up a $30K battery in the car.

Thanks!

zymurgic, 2022-10-20:
CCS protocol for DC is very different from the simple PWM protocols that OpenEVSE does for AC charging to communicate with the vehicle's on-board charger. For a start, it will communicate via a powerline network over the CP pin.  There's a lot of reading to be done of the official standards.

I wish you all the best of luck, it's not going to be easy.

JohnGalt1717, 2022-10-20:
A couple of things here just if anyone else is thinking about this problem:

1. Tesla I believe uses CANBus which should be MUCH easier to work with.
2. ST has full sample units on their site that will do charging over CCS. Considering buying one because they come without the DC/DC converter.  The problem then becomes not the car, but communicating with the ST board to tell it max current draw etc.

strohrbaugh, 2023-02-24:
I'm interested in doing something similar, too. Have you developed this any further?

JohnGalt1717, 2023-02-24:
I've found the following:

Tesla was using CAN but now uses Power Communications and indeed uses the same protocol as CCS.
There are off the shelf Power Communications systems.

The basic flow would be:

1. Plug in
2. Negotiate (PP, PE etc.)
3. Establish communication over IP
4. Talk via IP to negotiate voltage and amperage.
5. End if PP/PE or IP request.

Charger would be:

1. DC in. (or PFC to DC)
2. DC/DC boost (or buck depending)
3. MCU that talks over IP and Power Communication Protocol that controls the boost converter.
4. Various sense pins for PP and PE.

The hardest part of this is actually the IP link and coms.

JohnGalt1717, 2023-02-25:
You’re still losing dc to ac and then ac to dc doing this and if you use an off the shelf transformerless inverter you’re not going to gain a thing.

You’re at best at about 87% efficiency that way.

The reason to do dc/dc is that you can get into the 97-98% efficiency with a synchronous buck/boost.

strohrbaugh, 2023-02-25:
Oh I completely agree, but I haven't yet solved the comms problem that you articulated above. The DC-AC solution "solves" it, but admittedly quite poorly. Let you know if I come across any improvements using something approximately off-the-shelf.

JohnGalt1717, 2023-02-25:
There's a company that the Electric Viking on YouTube referenced that has a DC/DC charging solution coming.  I can't find anything about them.  But it's a lead.

strohrbaugh, 2023-02-25:
Thanks, that's a good start.

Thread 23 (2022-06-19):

Help identify OpenEVSE board

mat02, 2022-06-19:
Hi!
I have an OpenEVSE-based charger that I bought with the car. It's a DIY build, so I don't have any info about it. I would like to update the firmware and add WiFi module. Unfortunately, I am not sure which version of the firmware will be compatible with this board as I cannot find it anywhere in the Github repository. Can you please help me identify this board? Board is made out of two PCBs, the lower one is a 12V power supply, the upper one has uC and all the control pins.
Best regards,
Mateusz

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

martiinezz, 2022-06-19:
Skoro ma diodę to raczej kompatybilne z wersją 3 sprzętu. Która wersja FW obecnie tam siedzi?

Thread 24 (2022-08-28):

Short-circuit on AC output results in current transformer burden resistor failure.

kyang014, 2022-08-28:
During testing, I induced a short circuit on AC output of a OpenEVSE Advanced kit with controller hardware V5. The upstream circuit breaker tripped, but the event appears to have caused R26 to fail open. On subsequent charge attempts, the sensed current value was 100A+ despite the real current being 16A. Overcurrent faults were thrown as a result and charging stopped.

The current transformer itself tested normal and output a voltage corresponding to the correct 16A when measured out-of-circuit with a known good burden resistor. The 2.5V divider on the controller was also working.

The controller operates normally when R26 was replaced. Presumably, the spike of current through the CT during the short circuit induced a high voltage across the CT output. Suggest clamping the voltage across R26 to protect both it and the ATMEGA.

kyang014, 2022-08-28:
Potentially could be reproduced by using a bench power supply to apply a pulse of current to a wire wound around the CT many times to multiply the sensed current.

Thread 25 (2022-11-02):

Time to ditch the 328P for an RP2040 or something purchasable?

DrFrankReade, 2022-11-02:
Leaving the certification problem for another time.

I feel it's time for a hardware refresh, esp. a new MCU, and maybe spread the board out a bit.

Can't buy the Arduinos anymore. I would not be surprised if the ATmega328 is extinct. Digikey only shows "marketplace" products which are in all likelihood counterfeit or pulls.  Plus, the existing code barely fits.

I'm not kidding when I say we're using RP2040 at work in place of SAM chips we can't buy anymore, and always having a good laugh about it.  They require a few more external parts and they run at lower voltages, but they're impressive pieces of hardware with incredible community.

Stock has got to be running low on the existing OpenEVSE boards to boot.

doanerock, 2022-12-31:
I am confused because the only microcontroller on the OpenEVSE is a esp32.  Are you referring to the OpenEVSE Programmer, because I am pretty sure you can use any FTDI programmer, so this is a non issue.

DrFrankReade, 2023-01-02:
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

Every OpenEVSE has one.

It's where THIS code runs...

[https://github.com/OpenEVSE/open_evse](url)

doanerock, 2023-01-03:
You are correct, my bad.  I had to bring up the schematic to find where it is located.  Looks like it is under the relay which is why I could not find it in the pictures.
It looks like there are plenty of ATMEGA168P-20AU in stock.

DrFrankReade, 2023-01-03:
The 328 is the one that's shipping, and that's what the .bin releases are compiled for. The 168 also has half the program space, and if I recall correctly, the current code barely fits the 328.

My OPINION, aside from easing the supply chain concerns, is that a heftier MCU would give a bit more headroom to put back the old LCD based UI, which I think is gone nowm, and missed by me at least, for redundancy's sake, because it's been my experience that when the ESP32 goes down, the charger goes squirrely and I either can or can't charge the car.

Unfortunately, to move to a little ARM chip would require a complete hardware rework, as most stuff maxes out at 3.3V nowadays, and of course then supporting two hardware revisions... but if you can't buy chips, you can't ship product.

There are other ATMEGA 8 bit chips - The 32U4 seems to have a lot of stock, and it's a popular chip, and there's also something called a atmega4808 and somebody's written a core for it too, although I have no idea how well it works.

My thoughts anyway.

KanyonKris, 2024-04-14:
What a difference a year makes. While Microchip does not recommend the ATmega328P for new designs (https://www.microchip.com/en-us/product/atmega328p), it appears to be available for a reasonable price. Mouser has 90k in stock at $2.30 @ 100 qty.

The recommended successor, ATmega328PB is cheaper. It is not a drop-in replacement, there are 4 pin reassignments that will require a PCB revision, but 328 code will run on it. (https://www.pololu.com/file/0J1464/Atmel-42559-Differences-between-ATmega328P-and-ATmega328PB_ApplicationNote_AT15007.pdf)
Mouser has 33k of the extended temperature version in stock for $1.46 @ 100 quantity.

martiinezz, 2024-04-15:
Why not ESP32, it has 2 cores - WiFi and BT available - so it could be also possible to read cars battery state via BT to let say charge to 80 or 90% as some EVs lack such option.

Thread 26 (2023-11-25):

openevse terminal no longer detects cars

monfiston, 2023-11-25:
HELLO
my openevse terminal no longer detects cars
I can however modify parameters in the openevse
I tested the type 2 charging cable: ok
I tested that the CP pilot cable reached the openevse motherboard

do you have any idea which component would be hs on the openevse board?

Mathopenevse, 2024-01-22:
Salut, est-ce que tu as pu régler ton problème depuis? Ça m'ait arrivé déjà après avoir flashé la carte mais au bout de plusieurs essais c'est rentré dans l'ordre

monfiston, 2024-01-22:
Non

Mathopenevse, 2024-01-23:
Tu es sous quelle version? Tu as essayé de flasher ta carte?

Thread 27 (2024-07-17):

what is the different 5.6 board and 5.5 board

flyrobot, 2024-07-17:
i just realized the board i bought is version 5.6.
What is the difference between 5.5 and 5.6 ? is any documentation for 5.6 ? such as schematic, pcb, etc

Thank you

chris1howell, 2024-07-17:
There is no meaningful difference. The 2 larger ICs were moved from top (through hole) to bottom (surface mount) due to better part availability.

flyrobot, 2024-07-18:
is it possible to get 5.6 on github ? its quite difficult to trace the problem on the pcb's 5.6 base 5.5 kicad source

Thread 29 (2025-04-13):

6.5.1 I2C connector reversed?

ptrauejr, 2025-04-13:
In looking at the diagrams I see that on 5.5 the I2C connector had the key (open side) facing towards the edge of the board and the sda (green) was on the left.  On 6.5.1 I see that the I2C connector had the key facing away from the closest edge of the board yet the SDA was still on the left.  Was the connector reversed, or is this an oversight?

I'm upgrading from a 5.6 to 6.5.1 and l just want to make sure I hook this up properly.

leothehuman, 2025-09-07:
My kit also looks  like the kit pictured above. I also believe the connector is mislabeled in both png and pdf schematics.

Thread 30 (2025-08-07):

Kit Assembly Layout OpenEVSE_PLUS_v6.5.1

martin3142, 2025-08-07:
Very good kit, thanks.

**1:**

For the present backplate layout, there is overly generous space left at the top of the case compared to the overly difficult cramped area at the bottom that must accommodate the heavy gauge cables...

See my assembly attempt!

To make the cabling easier, can the OpenEVSE module and relay both be moved equally towards the top of the base plate to give more room for cabling in the lower 1/3rd of the case?

**2:**

I placed the temperature sensor on the relay to give early warning of any problems with a (hot) resistive connection on the high current side. This is close to exposed mains terminals: Hence the use of insulation tape around the terminals to protect for if the sensor were to become detached/loose.

Are shrouds available for the mains terminals?

Thanks,
Martin

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

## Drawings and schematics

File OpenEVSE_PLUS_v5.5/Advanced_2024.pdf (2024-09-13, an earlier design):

## 5v i2c

## LCD/WiFi

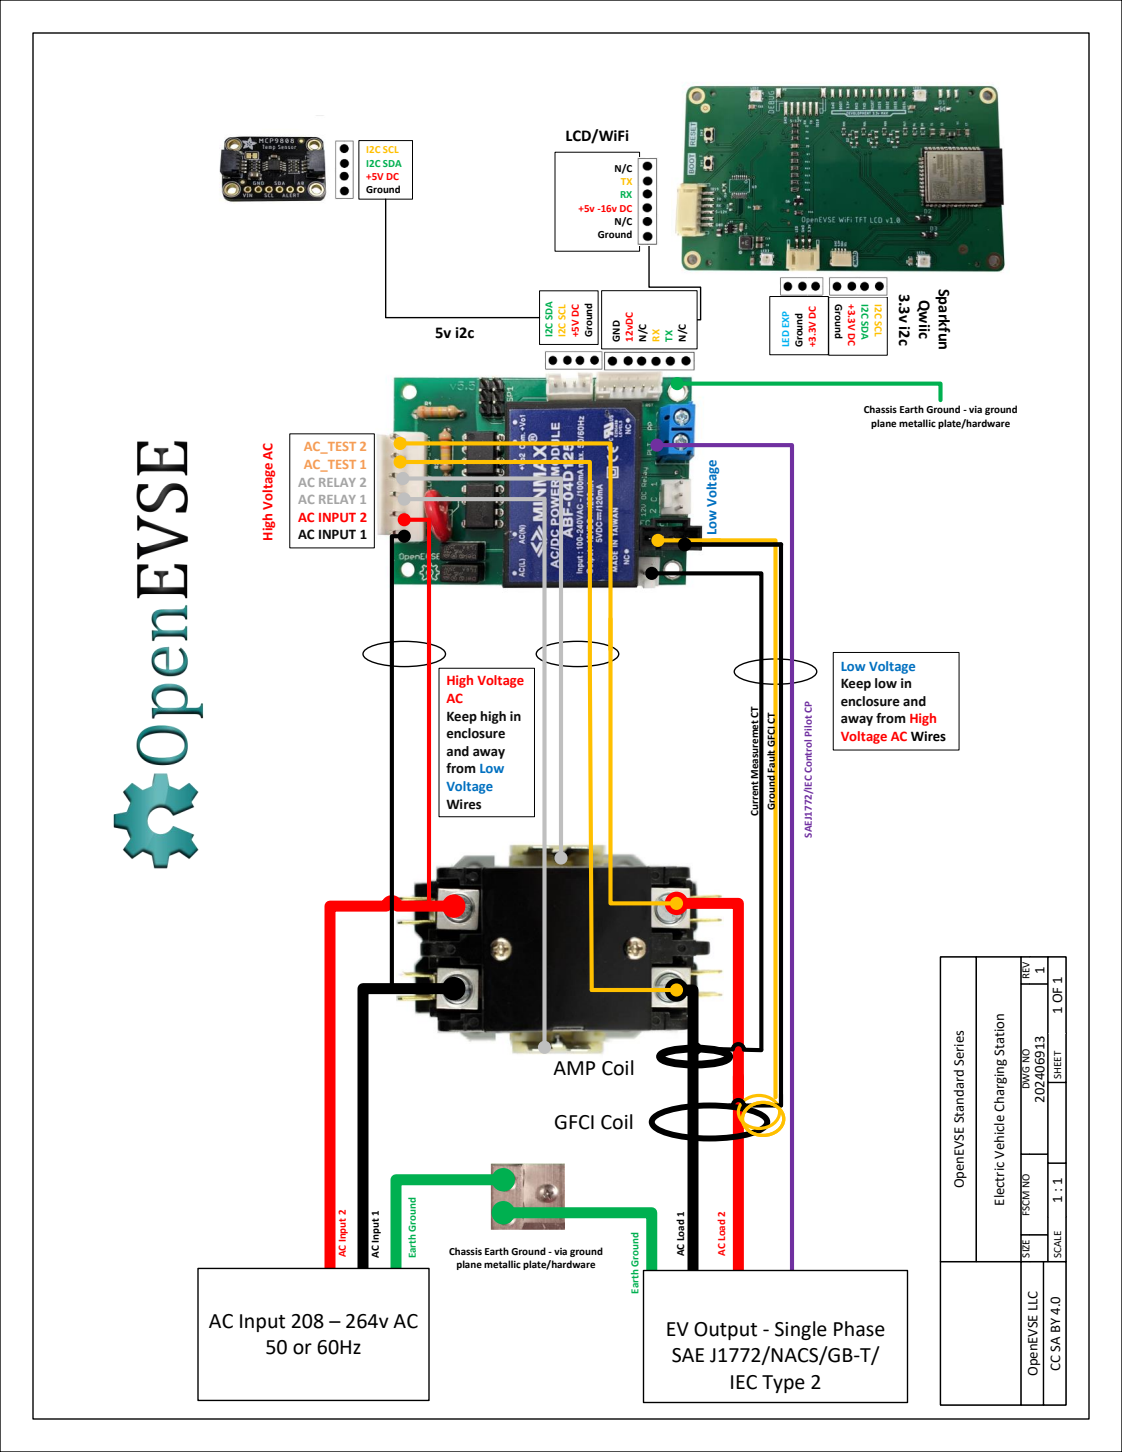
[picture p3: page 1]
I2C SDA; I2C SCL; Ground; I2C SCL I2C SDA +5V DC Ground; AC_TEST 2 AC_TEST 1 AC RELAY 2 AC RELAY 1 AC INPUT 2 AC INPUT 1; AC Input 2; AC Input 1; Earth Ground; AC Load 1; AC Load 2; OpenEVSE LLC; N/C TX RX +5v -16v DC N/C Ground; GFCI Coil; AMP Coil; GND; 12vDC; Sparkfun; Qwiic; LED EXP; Low Voltage

Chassis Earth Ground - via ground
plane metallic plate/hardware

High Voltage AC

Low Voltage
Keep low in
enclosure and
away from High
Voltage AC Wires

High Voltage
Keep high in
enclosure
and away
from Low
Voltage
Wires

Current Measuremet CT

SAEJ1772/IEC Control Pilot CP

Ground Fault GFCI CT

SIZE FSCM NO DWG NO REV

SCALE 1 : 1 SHEET 1 OF 1

Electric Vehicle Charging Station

OpenEVSE Standard Series

AC Input 208 – 264v AC

EV Output - Single Phase
SAE J1772/NACS/GB-T/
IEC Type 2

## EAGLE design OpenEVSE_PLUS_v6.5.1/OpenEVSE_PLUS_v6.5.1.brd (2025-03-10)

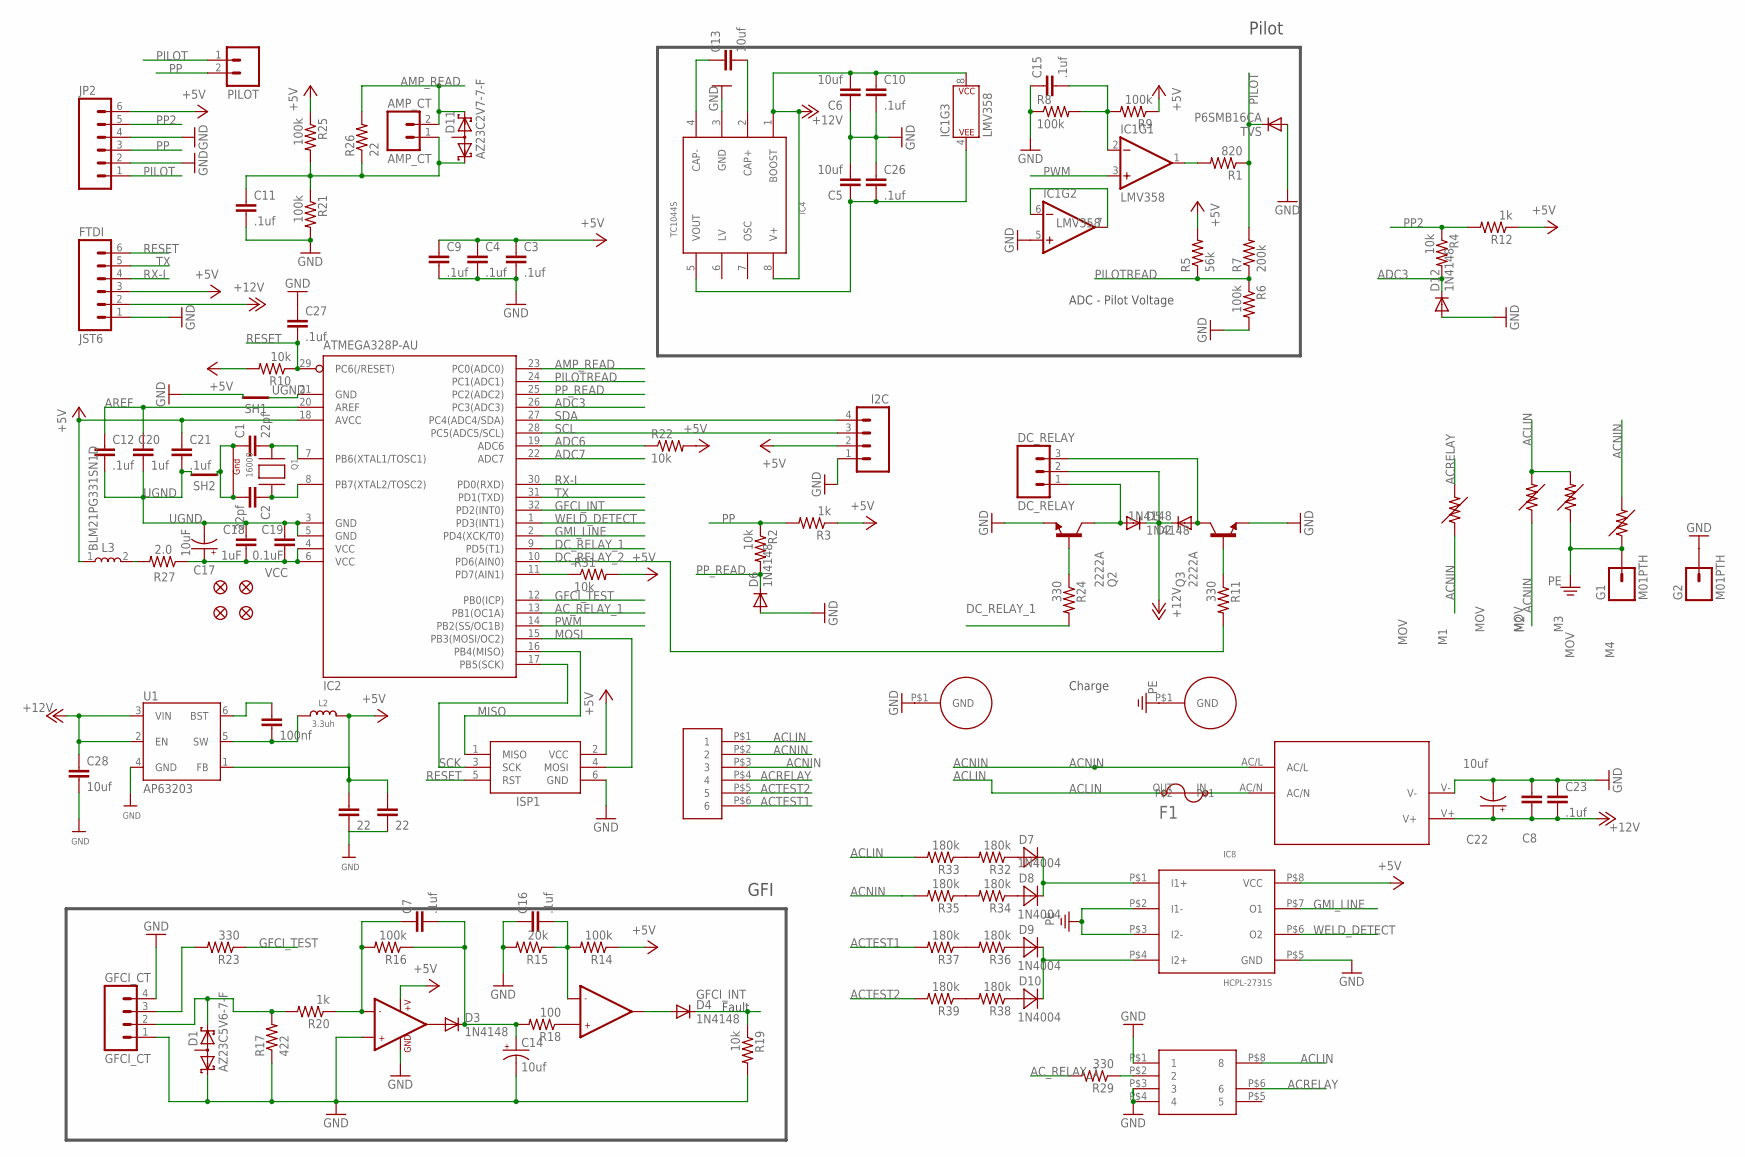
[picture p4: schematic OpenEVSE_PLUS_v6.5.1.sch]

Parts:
AC: JST-VH-6
AMP_CT: AMP_CT; MOLEX_2
C1, C2: 22pf; 0805
C3, C4, C7, C9, C10, C11, C12, C15, C16, C21, C23, C26, C27: .1uf; 0805
C5, C6, C13, C28: 10uf; 0805
C8, C20: 1uf; 0805
C14, C22: 10uf; EIA3216
C17: 10uF; 0603-POLAR
C18: 1uF; 0805
C19: 0.1uF; 0805
C29, C33: 22; 0805
C32: 100nf; 0805
D1: AZ23C5V6-7-F; SOT23
D2, D3, D4, D5, D6, D12: 1N4148; SOD123
D7, D8, D9, D10: 1N4004; SMA
D11: AZ23C2V7-7-F; SOT23
DC_RELAY: DC_RELAY; MOLEX_3
F1: BEL1.6AFUSE; BELFUSE1A
FID1, FID2, FID3, FID4: FIDUCIAL1X2.5; FIDUCIAL-1X2.5
FTDI: JST6
G1, G2: M01PTH; 1X01
GFCI_CT: GFCI_CT; GFCI_4
I2C: M04JST-PTH-VERT; JST-4-PTH-VERT
IC1: LMV358; SO08
IC2: ATMEGA328P-AU; TQFP32-08
IC3: LM358; SO08
IC4: TC1044S; SO-8
IC7: AQH2223; SIL8
IC8: HCPL-2731S; SIL8-2
ISP1: ISP1; AVRISP
JP2: M06POLAR_LOCK; MOLEX-1X6_LOCK
L2: 3.3uh; MICROBUILDER_INDUCTOR_5X5MM_NR5040_NOTHERMALS
L3: BLM21PG331SN1D; INDC2012X87
M1, M2, M3, M4: MOV
PILOT: M025MM; SCREWTERMINAL-5MM-2
PS1: IRM-10-5
Q1: 16000; NX3225
Q2, Q3: 2222A; SOT23
R1: 820; 0805
R2, R4, R10, R19, R22, R31: 10k; 0805
R3, R12, R20: 1k; 0805
R5: 56k; 0805
R6, R8, R9, R14, R16, R21, R25: 100k; 0805
R7: 200k; 0805
R11, R23, R24, R29: 330; 0805
R15: 20k; 0805
R17: 422; 0805
R18: 100; 0805
R26: 22; R1206
R27: 2.0; 0805
R32, R33, R34, R35, R36, R37, R38, R39: 180k; 1210
SH1, SH2: SHORT-HT5; SHORT_TOP-50
TVS: P6SMB16CA; SMB
U1: AP63203; SOT23-6
U$3, U$9: HOLE

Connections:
+5V: C3.1, C4.1, C9.1, C21.1, C29.1, C33.1, FTDI.3, I2C.2, IC2.18 (AVCC), IC3.8 (+V), IC8.P$8 (VCC), ISP1.2 (VCC), JP2.6, L2.P$2 (2), L3.1, R3.1, R5.2, R9.1, R10.2, R12.1, R14.1, R22.2, R25.1, R31.2, U1.1 (FB)
+12V: C6.2, C8.1, C10.1, C22.A (+), C23.2, C28.1, D2.C, D5.C, DC_RELAY.2, FTDI.2, IC1.8 (P$V+), IC4.1 (BOOST), IC4.8 (V+), PS1.V+, U1.2 (EN), U1.3 (VIN)
-12V1: C5.1, C26.2, IC1.4 (P$V-), IC4.5 (VOUT)
ACLIN: AC.P$1 (1), F1.OUT, IC7.P$8 (8), M2.P$2 (2), M3.P$2 (2), R33.2
ACNIN: AC.P$2 (2), AC.P$3 (3), M1.P$1 (1), M2.P$1 (1), M4.P$2 (2), PS1.AC/L, R35.2
ACRELAY: AC.P$4 (4), IC7.P$6 (6), M1.P$2 (2)
ACTEST1: AC.P$6 (6), R37.2
ACTEST2: AC.P$5 (5), R39.2
AC_RELAY_1: IC2.13 (PB1(OC1A)), R29.2
ADC3: D12.C, IC2.26 (PC3(ADC3)), R4.2
ADC6: IC2.19 (ADC6), R22.1
ADC7: IC2.22 (ADC7)
AMP_READ: AMP_CT.2, D11.2 (K2), IC2.23 (PC0(ADC0)), R26.2
AREF: C12.1, C20.1, IC2.20 (AREF)
DAMP: L3.2, R27.2
DC_RELAY_1: IC2.9 (PD5(T1)), R24.2
DC_RELAY_1_O: D5.A, DC_RELAY.1, Q2.3 (C)
DC_RELAY_1_T: Q2.1 (B), R24.1
DC_RELAY_2: IC2.10 (PD6(AIN0)), R11.2
DC_RELAY_2_O: D2.A, DC_RELAY.3, Q3.3 (C)
DC_RELAY_2_T: Q3.1 (B), R11.1
GFCI_INT: D4.C, IC2.32 (PD2(INT0)), R19.1
GFCI_TEST: IC2.12 (PB0(ICP)), R23.1
GFI_TEST_O: GFCI_CT.3, R23.2
GMI_LINE: IC2.2 (PD4(XCK/T0)), IC8.P$7 (O1)
GND: C3.2, C4.2, C5.2, C6.1, C8.2, C9.2, C10.2, C11.2, C14.C (-), C15.1, C16.1, C22.C (-), C23.1, C26.1, C27.1, C28.2, C29.2, C33.2, D1.1 (K1), D6.A, D12.A, FTDI.1, G2.1, GFCI_CT.1, GFCI_CT.4, I2C.1, IC1.5 (+IN), IC3.3 (+IN1), IC3.4 (GND), IC4.3 (GND), IC7.P$1 (1), IC7.P$3 (3), IC7.P$4 (4), IC8.P$5 (GND), ISP1.6 (GND), JP2.2, JP2.4, PS1.V-, Q2.2 (E), Q3.2 (E), R6.2, R8.1, R15.2, R17.1, R19.2, R21.2, SH1.2, TVS.A, U1.4 (GND), U$9.P$1
MISO: IC2.16 (PB4(MISO)), ISP1.1 (MISO)
MOSI: IC2.15 (PB3(MOSI/OC2)), ISP1.4 (MOSI)
unnamed: D9.C, D10.C, IC8.P$4 (I2+)
unnamed: D7.C, D8.C, IC8.P$1 (I1+)
unnamed: C1.2, IC2.7 (PB6(XTAL1/TOSC1)), Q1.2 (X1)
unnamed: C2.1, IC2.8 (PB7(XTAL2/TOSC2)), Q1.4 (X2)
unnamed: D7.A, R32.1
unnamed: AMP_CT.1, C11.1, D11.1 (K1), R21.1, R25.2, R26.1
unnamed: C7.1, IC3.2 (-IN1), R16.2, R20.1
unnamed: D8.A, R34.1
unnamed: C15.2, IC1.2 (-IN), R8.2, R9.2
unnamed: IC1.1 (OUT), R1.2
unnamed: IC2.11 (PD7(AIN1)), R31.1
unnamed: R32.2, R33.1
unnamed: IC1.6 (-IN), IC1.7 (OUT)
unnamed: C32.1, U1.6 (BST)
unnamed: C32.2, L2.P$1 (1), U1.5 (SW)
unnamed: R34.2, R35.1
unnamed: IC7.P$2 (2), R29.1
unnamed: C13.2, IC4.2 (CAP+)
unnamed: D1.2 (K2), GFCI_CT.2, R17.2, R20.2
unnamed: D3.A, IC3.1 (OUT1)
unnamed: R36.2, R37.1
unnamed: C7.2, C14.A (+), D3.C, R16.1, R18.2
unnamed: C16.2, IC3.6 (-IN2), R14.2, R15.1
unnamed: D4.A, IC3.7 (OUT2)
unnamed: IC3.5 (+IN2), R18.1
unnamed: C13.1, IC4.4 (CAP-)
unnamed: R38.2, R39.1
unnamed: D9.A, R36.1
unnamed: D10.A, R38.1
unnamed: F1.IN, PS1.AC/N
PE: G1.1, IC8.P$2 (I1-), IC8.P$3 (I2-), M3.P$1 (1), M4.P$1 (1), U$3.P$1
PILOT: JP2.1, PILOT.1, R1.1, R7.2, TVS.C
PILOTREAD: IC2.24 (PC1(ADC1)), R5.1, R6.1, R7.1
PP: JP2.3, PILOT.2, R2.1, R3.2
PP2: JP2.5, R4.1, R12.2
PP_READ: D6.C, IC2.25 (PC2(ADC2)), R2.2
PWM: IC1.3 (+IN), IC2.14 (PB2(SS/OC1B))
RESET: C27.2, FTDI.6, IC2.29 (PC6(/RESET)), ISP1.5 (RST), R10.1
RX-I: FTDI.4, IC2.30 (PD0(RXD))
SCK: IC2.17 (PB5(SCK)), ISP1.3 (SCK)
SCL: I2C.3, IC2.28 (PC5(ADC5/SCL))
SDA: I2C.4, IC2.27 (PC4(ADC4/SDA))
TX: FTDI.5, IC2.31 (PD1(TXD))
UGND: C12.2, C17.-, C18.1, C19.1, C20.2, C21.2, IC2.3 (GND), IC2.5 (GND), IC2.21 (GND), SH1.1, SH2.2
VCC: C17.+, C18.2, C19.2, IC2.4 (VCC), IC2.6 (VCC), R27.1
WELD_DETECT: IC2.1 (PD3(INT1)), IC8.P$6 (O2)
XGND: C1.1, C2.2, Q1.1 (G1), Q1.3 (G2), SH2.1

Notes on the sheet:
Pilot
ADC - Pilot Voltage
Charge
Fault
GFI

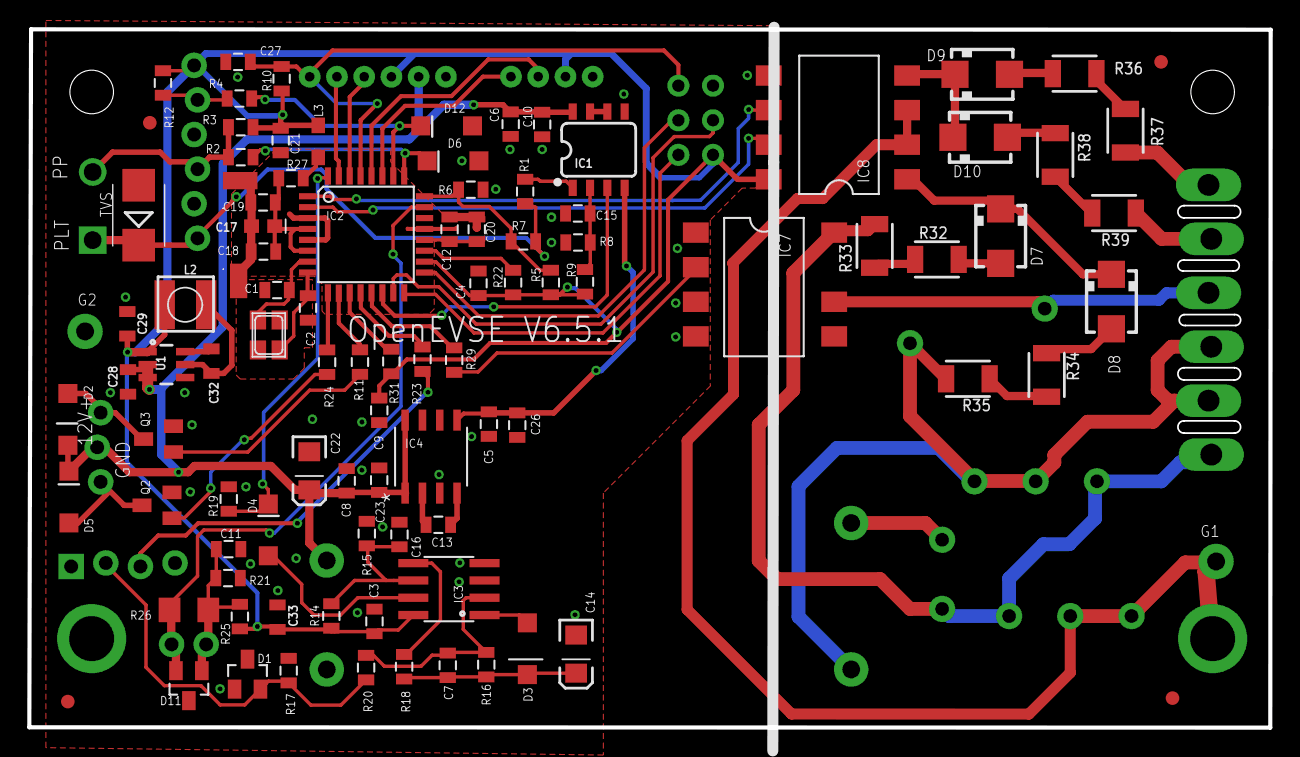
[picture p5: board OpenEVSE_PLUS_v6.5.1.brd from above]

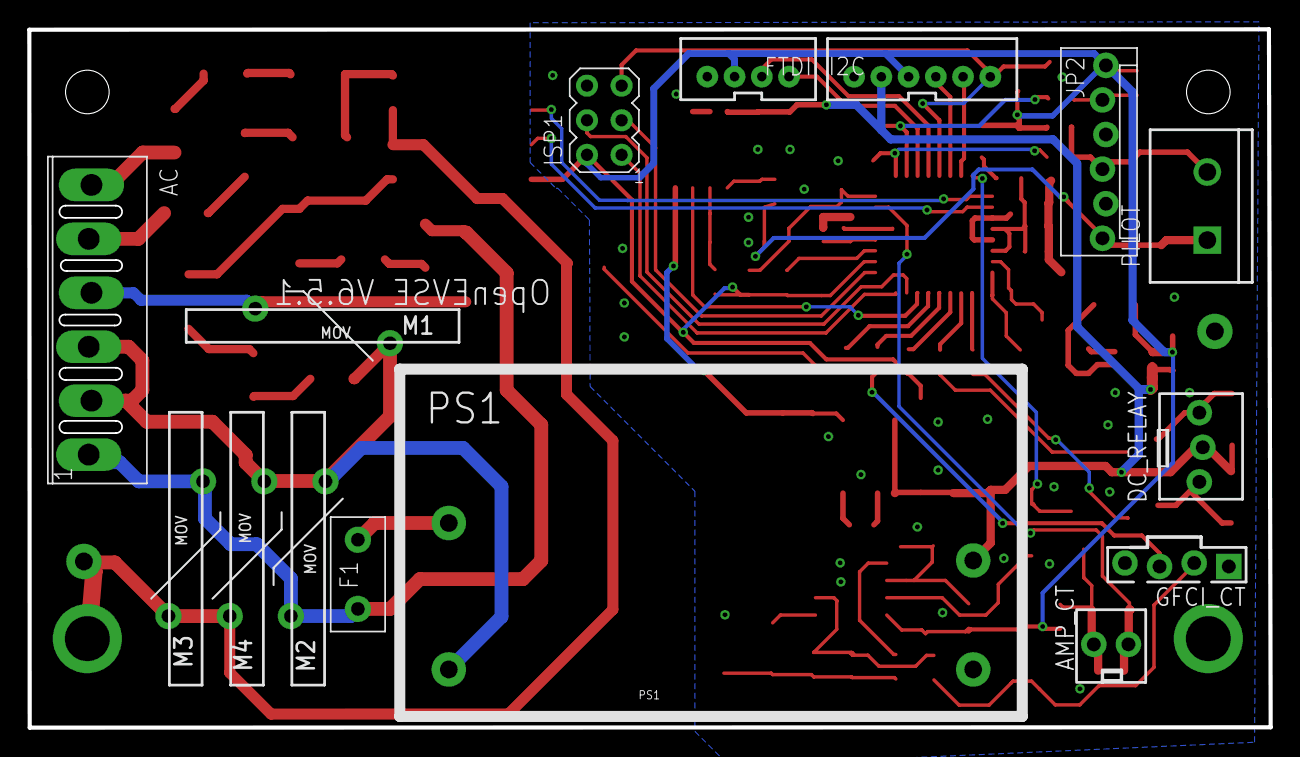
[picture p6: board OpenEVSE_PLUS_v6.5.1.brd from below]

Board: 2 copper layers, 91.1 x 51.3 mm, 115 parts (15 on the bottom side), 74 nets.

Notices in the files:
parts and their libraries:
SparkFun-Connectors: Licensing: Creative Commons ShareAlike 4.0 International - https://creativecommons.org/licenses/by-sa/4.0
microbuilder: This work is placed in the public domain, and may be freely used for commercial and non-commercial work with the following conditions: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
